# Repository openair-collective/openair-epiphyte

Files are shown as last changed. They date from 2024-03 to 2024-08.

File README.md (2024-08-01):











# Epiphyte

## Introduction

Epiphyte is a miniature, stand-alone, open source direct air capture machine that removes CO2 from the air, designed by OpenAir volunteers.

The name "Epiphyte" comes from the same term referring to a plant that grows on the surface of another plant. The "host plant" here is Thursday ([YouTube intro](https://www.youtube.com/watch?v=E_M0lsxscfE)), a previous generation carbon capture device designed by the team at Octavia Carbon of Kenya.

There are two main goals of the Epiphyte device:

1. __To reproduce Thursday in an alternate form in order to provide sufficient documentation to rebuild such a device.__ Thursday is an older generation carbon capture device. It is no longer in active development, and was to be used as an example to propagate build iterations in other locations. However, parts of Thursday still could not be disclosed, and the purpose of the Epiphyte build was to untangle very technical details of Thursday so that clear documentation can be created for next generation Thursday builders.

1. __To create a modular venue for testing sorbents.__ Although not a major purpose of Epiphyte, the recipe for Thursday cannot be disclosed exactly. Epiphyte is built so that the sorbent could be swapped out to study the behavior of different ones, if needed.

For further background information see the [links section](#links).

### Current state of the work

The original Epiphyte was built in Philadelphia, and University of Pennsylvania is home to it. The next potential steps depend on the data collected from this device, including:
- Heating and temperature control and feedback
- Carbon dioxide sensing--whether the current sensors are adequate
- Use of basic sorbents

From this data, knowledge of the mechanics of the device can be extracted. Depending on the ultimate goal of the device, i.e., research vs commercial vs "maker-ware", Epiphyte can be further improved, or elements of it can be borrowed in a completely new device.

## About this repository

This repository attempts to collect all relevant design files, documentation, and links, and presents them as a package of material that can be used to gain a viable amount of knowledge toward understanding the mechanics of Thursday.

The root folder has the following subdirectories:

```sh
.
├── hardware_files/
├── license_info/
├── presentations/
└── software/
```

### `presentations`

The PowerPoint presentations here include background information and schematics from throughout the build process. Schematics of the entire built system, photos of the build process, as well as preliminary data can be found throughout the slides.

If looking for an introduction to Epiphyte, looking at these presentations first is recommended.

### `license_info` and `LICENSE.txt`

The files in the folder explain how to use the material in this repository for further development. The technology is open-sourced (license text), but a few instructions (`license_info/cern_ohl_p_v2_howto.pdf`) need to be followed for material reuse.

### `software`

Includes Arduino code for controlling heating and reading from sensors on Epiphyte.

### `hardware`

This section has bills of materials (BOM) as well as a list of 3D components that can be used to create 3D assemblies. See the [hardware README](hardware_files/README.md) for more details and supplemental links.

## Links

#### YouTube videos

- [About Octavia Carbon's Thursday](https://www.youtube.com/watch?v=E_M0lsxscfE)
- [Live walkthrough of Thursday](https://www.youtube.com/watch?v=BNXJqeISVzQ)
- Epiphyte webinars
    - [Episode 1 - Intro and build launch](https://www.youtube.com/watch?v=B53BWDbAE4Q)
    - [Episode 2 - Assembly report](https://www.youtube.com/watch?v=-oX7TFdO3ws)
    - [Episode 3 - Sorbent panel progress](https://www.youtube.com/watch?v=SeYeDm23_dI)
    - [Epiphyte @ COP28](https://www.youtube.com/watch?v=A-t8T-azwP8)

#### Other

- [Epiphyte on OpenAir forums](https://www.openairforum.org/c/rd/epiphyte/106)
- [Epiphyte on Hackster.io](https://www.hackster.io/epiphyte/epiphyte-open-direct-air-capture-d55a9e)
- [First build on Carbon Crowd website](https://carboncrowd.cc/builds/vvRHB4d3vJyN1Ihpj5yi)

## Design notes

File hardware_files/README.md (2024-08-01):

# Hardware

## Hardware Description
The Hardware Description folder includes high-level documentation of how the parts are connected, as well as pinouts and engineering notes for different classes of components. Make sure to read [that documentation](HW%20Description/README.md) to see how the system is assembled. 

## Bills of Materials (BOMs)

A BOM is a list of materials needed to reproduce the physical device as closely as possible. There are two BOM files:

- Sorbent Panel and CO<sub>2</sub> Sensor Box
- Electronics and HVAC

Each list includes information on obtaining the materials, including vendors, pricing, whether customization is needed.

In the sorbent panel BOM, there are also a `Item ID` column that corresponds to individual 3D CAD files. There are two tabs in this file--one that lists off-the-shelf components (IDs that start with `M`), and the other that lists custom components (IDs that start with `C`).

### CAD files for sorbent panel and CO<sub>2</sub> sensor box components

3D CAD files for individual components, either in `.step` or `.sldprt` format, are available for most line items. These files include those for off-the-shelf components (for convenience) and custom components (required for repeat fabrication by a machine shop). The CAD file names are preceded by the `Item ID` so that they can be matched up to the line item easily. The anatomy of the CAD file names is as follows:

`{Item ID}_{Vendor Name}_{Part Number}_{Part Description}.{Extension}`

For custom parts, the file name is simply:

`{Item ID}_{Part Description}.{Extension}`

Some custom parts are provided with multiple formats of fabrication files, including 2D and 3D CAD files. 2D files may come in two versions--with and without holes--in case one wants to drill holes themselves, e.g., to save cost or for hole size flexibility.

CAD files of all custom parts are accessible, at the time of the publication of this repository, in live-maintained [Onshape](https://www.onshape.com/) files. The BOM lists links for finding the Onshape version of each custom file. The assemblies can be found here: [sorbent panel](https://cad.onshape.com/documents/3e513bed349fbe5dac3c2097/w/f4ba0cf31e493613401f5693/e/31d268d611fa49f66a7aafab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) and [sensor box](https://cad.onshape.com/documents/c282863293f77fd9e75ee4bd/w/2c50dc42efc36e588e65a721/e/b7f233adbe17413331fabfa8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)

Note: Onshape is free to use for non-commercial/hobby purposes. The files are free to access and download, although they may need an Onshape account to fork (in the same way software repos are forked).

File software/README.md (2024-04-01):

# Software

Software includes mainly Arduino code for controlling heating and sensors 
during capture of carbon.

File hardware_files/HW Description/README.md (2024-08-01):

# Epiphyte Electronic Hardware Description

## Overview
This document serves as a reference for the electronic hardware elements of the first prototype of Epiphyte. The design evolved as it was built, and I offer suggestions for improvement or modifications as appropriate.
In the interest of brevity, it is assumed that the reader is already familiar with electronics and programming.

### Epiphyte System
The overall design of the Epiphyte system is shown in Figure 1, below, with a focus on the elements to be described in this document.
 
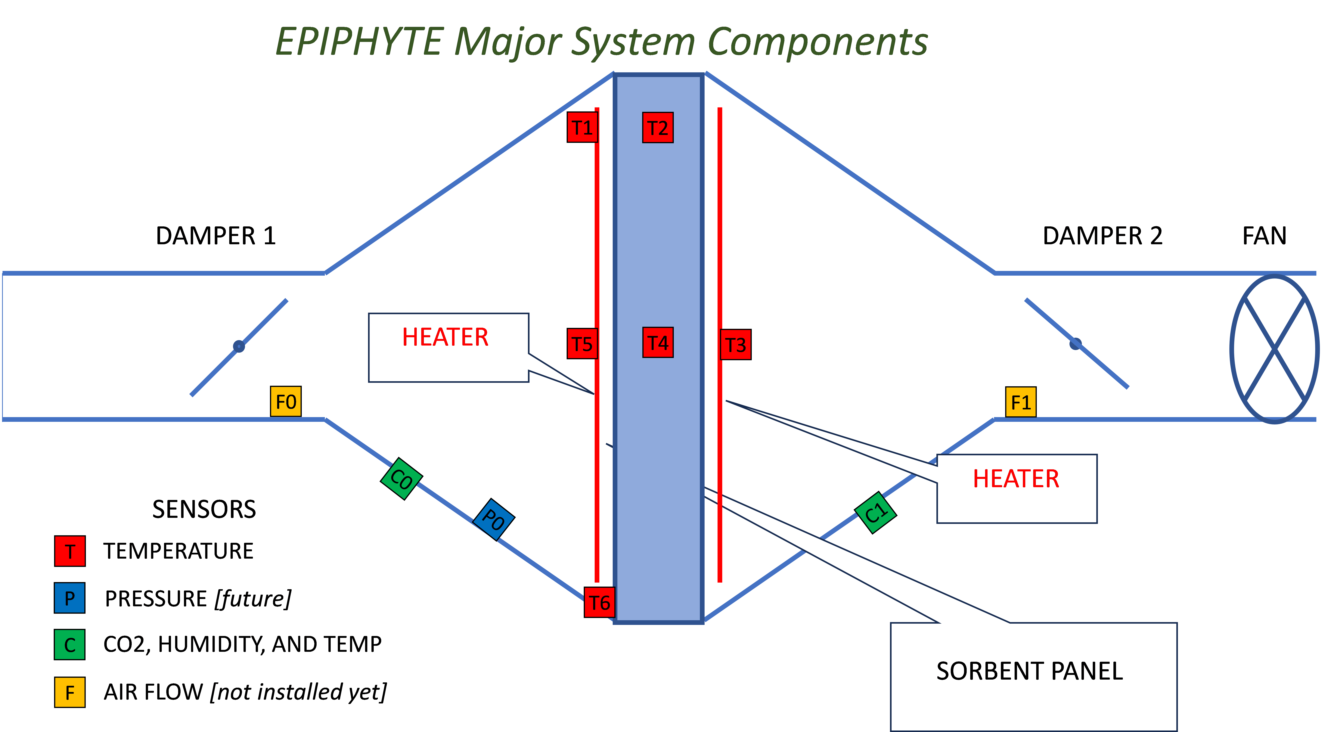
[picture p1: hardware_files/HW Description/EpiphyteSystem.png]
Epiphyte block diagram


### Electronics Block Diagram
To put the detailed description that follows into context, we include a high-level block diagram of Epiphyte’s electrical circuitry. 
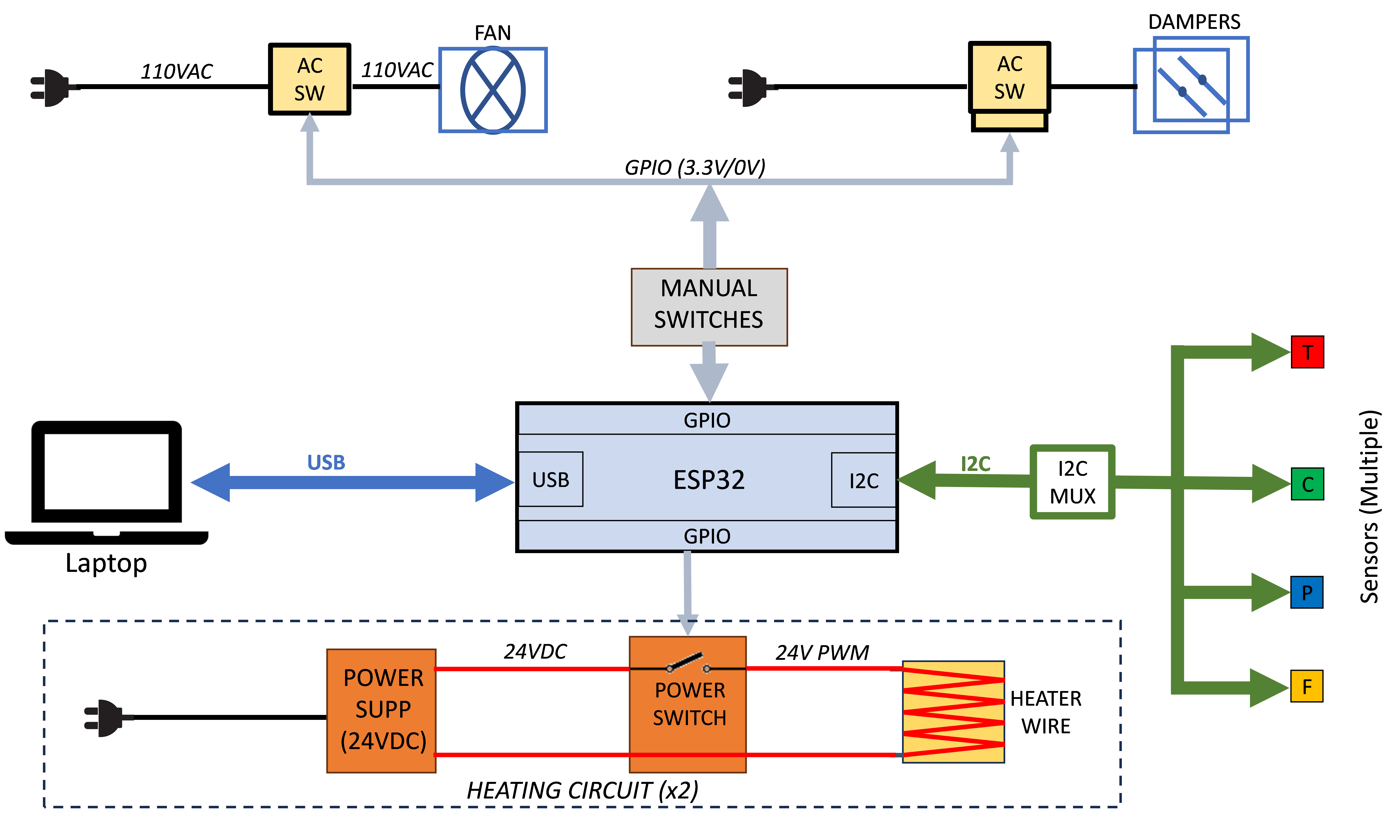
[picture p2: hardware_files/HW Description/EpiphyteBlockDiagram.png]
Epiphyte electrical block diagram


## Processor
The processor is an [Adafruit ESP32 Feather V2](https://www.adafruit.com/product/5400). Most other processors should work, as the application is not critical for speed or complex calculations. In particular, most 3.3-V processors of the Arduino or Adafruit Feather family should work with a few changes to the software. (Don’t use a 5V processor unless you know what you’re doing!) The processor also includes WiFi and Bluetooth connectivity, but these features have not been employed with Epiphyte as of this writing. They might be useful for data logging onto a server, or for remote control and monitoring of the system.

The user is urged to read and understand the information provided by Adafruit here: https://learn.adafruit.com/adafruit-esp32-feather-v2

The Feather can be programmed either in C/C++ or Python. In Epiphyte, I used C/C++.

### Pinout
Design files and pinouts for the board can be found here: https://github.com/adafruit/Adafruit-ESP32-Feather-V2-PCB/tree/main 
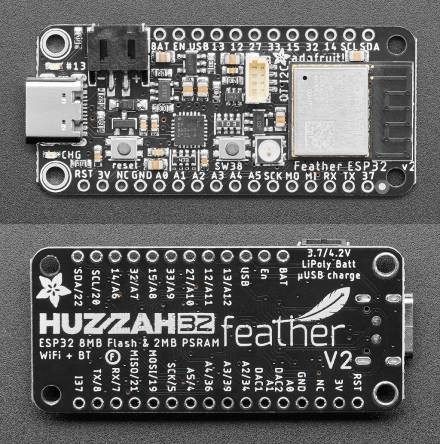
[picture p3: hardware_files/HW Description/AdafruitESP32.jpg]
Top and bottom of Adafruit ESP32 circuit board.
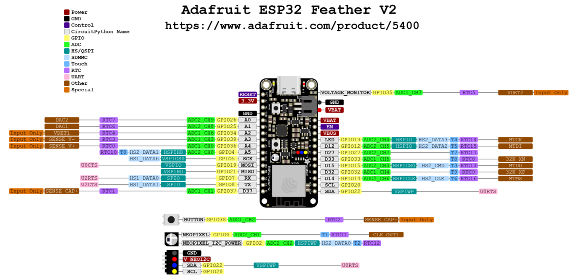
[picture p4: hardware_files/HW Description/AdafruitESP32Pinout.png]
Pinout diagram for Adafruit ESP32 circuit board.
 

### Display
For realtime monitoring of system activity, a monochrome OLED display is provided. This [Adafruit Featherwing](https://www.adafruit.com/product/4650) can be attached to the Feather processor. All connections are made through pins without needing any additional wiring. 
Communication with the display is via I2C, and this board also includes three pushbutton switches that are connected to processor GPIO pins. These could be useful for real-time control of the system.

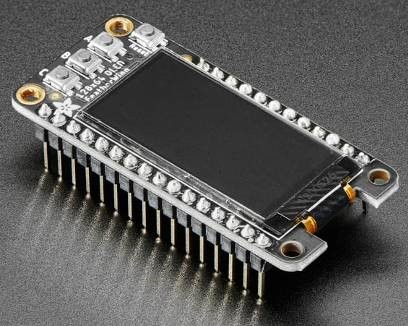
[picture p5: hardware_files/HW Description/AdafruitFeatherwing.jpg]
Image of Adafruit Featherwing OLED display.


### NeoPixel
An RGB LED (“Neopixel”) is supplied on the Feather board. This LED’s color and brightness can be programmed and used as a visual indicator. The NeoPixel library handles all the programming of this device.

### Processor Pin Assignments
This table shows the GPIO pins that are used in this design. Functions are detailed in sections below.
| Pin No | Signal | In/Out | Description |
|---|---|---|---|
| 0 | NEOPIXEL_PIN | O | Serial communication with NeoPixel |
| 12 | swRUN | I | To toggle switch: active LOW sets RUN mode |
| 13 | swSET | I | To toggle switch: active LOW sets SETUP mode |
| 14 | BUTTON_C | I | To OLED board pushbutton C (not used) |
| 15 | BUTTON_A | I | To OLED board pushbutton A (not used) |
| 27 | HEAT_PWM_1 | O | To Heater 1 control gate; PWM duty-cycle control |
| 32 | BUTTON_B | I | To OLED board pushbutton A (not used) |
| 33 | HEAT_PWM_2 | O | To Heater 2 control gate; PWM duty-cycle control |

## I2C Connections
The sensors in Epiphyte are all connected to the processor with the [I2C](https://en.wikipedia.org/wiki/I%C2%B2C) serial bus.  It is important to note that because the processor supply and interfaces are 3.3V, any slave devices must also operate from this voltage (including pullups) to avoid damaging the processor.

### Stemma QT
[STEMMA QT](https://learn.adafruit.com/introducing-adafruit-stemma-qt/what-is-stemma-qt) is an Adafruit system for easily making I2C connections between compatible devices. Many boards come with a STEMMA QT connector, and cables of various lengths are available to connect devices simply by plugging in the cables. 
Each cable has 4 wires: Power, Ground, SDA, and SCK. Cables come in various lengths; an example is depicted below.
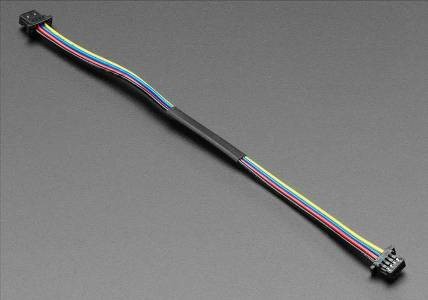
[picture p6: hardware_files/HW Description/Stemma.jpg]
Photograph of Adafruit Stemma QT cable.


### I2C Extender
I2C signals suffer degradation with longer cables (including STEMMA QT cables). The [I2C extender](https://www.adafruit.com/product/4756) allows cascades of STEMMA QT cables or longer runs between the processor and the sensors. The LTC4311 is an IC which boosts and reshapes I2C signals, and is available from Adafruit on a breakout board with convenient STEMMA QT connectors. This device is liberally used in Epiphyte wherever longer signal runs are needed.
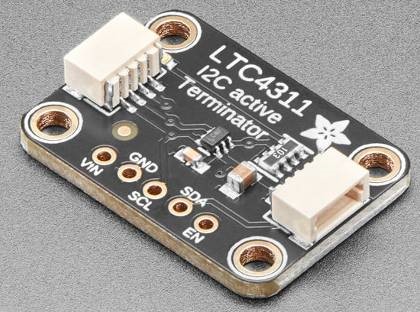
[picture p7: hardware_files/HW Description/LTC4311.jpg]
Adafruit LTC4311 I2C Extender breakout board.


### I2C Multiplexing
Because there are multiple instances of each type of sensor, most with fixed I2C addresses, a multiplexer is necessary to disambiguate these devices for correct addressing. Adafruit makes a [breakout board](https://www.adafruit.com/product/5626) for the PCA9548 I2C multiplexer chip (shown below), which features a common port on the end and eight switched ports around two edges, all with STEMMA QT connectors.

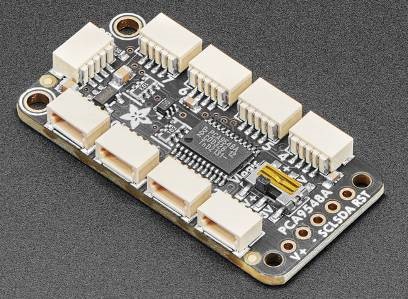
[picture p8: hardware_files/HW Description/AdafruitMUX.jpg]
Photograph of Adafruit 1:8 mux.


The MUX acts as a bidirectional 1-to-8 switch, and is itself an I2C device with its own address. The I2C address of the MUX can be selected with solderable jumpers on the PCB (labelled A0, A1, and A2 on the back - see image below). The position of the switch is controlled by the processor sending a formatted command. Then the MUX becomes transparent and the selected slave device can be addressed in the usual way as if it were the only one on the bus with that address. Note that the ports are numbered 0 through 7.

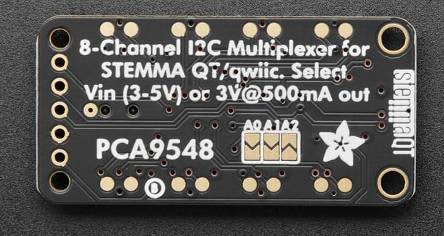
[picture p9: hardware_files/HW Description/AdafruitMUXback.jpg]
Photograph of Adafruit 1:8 mux breakout board, back side.


In the current embodiment of Epiphyte, two 1:8 MUXes are used, with labels as used in the software and corresponding addresses as follows:
| MUX Label | MUX I2C Address |
|---|---|
| MUX1 | 0x71 |
| MUX2 | 0x72 |

The MUX addresses and port numbers of each sensor used in Epiphyte are shown in this table and in the schematic below:
| Device | Part No. | Label | MUX# | MUX Channel | Device I2C Address | Location |
|---|---|---|---|---|---|---|
| Thermocouple Amp | MCP9600 | T0 | 2 | 0 | 0x67 | Not used |
| Thermocouple Amp | MCP9600 | T1 | 2 | 1 | 0x67 | Input side heater wire, corner |
| Thermocouple Amp | MCP9600 | T2 | 2 | 2 | 0x67 | Sorbent center, corner |
| Thermocouple Amp | MCP9600 | T3 | 2 | 3 | 0x67 | Output side heater wire, center |
| Thermocouple Amp | MCP9600 | T4 | 2 | 4 | 0x67 | Sorbent center, center |
| Thermocouple Amp | MCP9600 | T5 | 2 | 5 | 0x67 | Input side heater wire, center |
| Thermocouple Amp | MCP9600 | T6 | 2 | 6 | 0x67 | Sorbent frame |
| Thermocouple Amp | MCP9600 | T7 | 2 | 7 | 0x67 | Not used |
| CO2 Sensor | SCD30 | C0 | 1 | 3 | 0x61 | Input duct |
| CO2 Sensor | SCD30 | C1 | 1 | 4 | 0x61 | Output duct |
| Pressure Sensor | MPRLS | P0 | 1 | 5 | 0x18 | Not used (yet) |
| Flow meter | FS1015-1005 | F0 | 1 | 2 | 0x50 | Not used (yet) |
| Flow meter | FS1015-1005 | F1 | 1 | 1 | 0x50 | Not used (yet) |

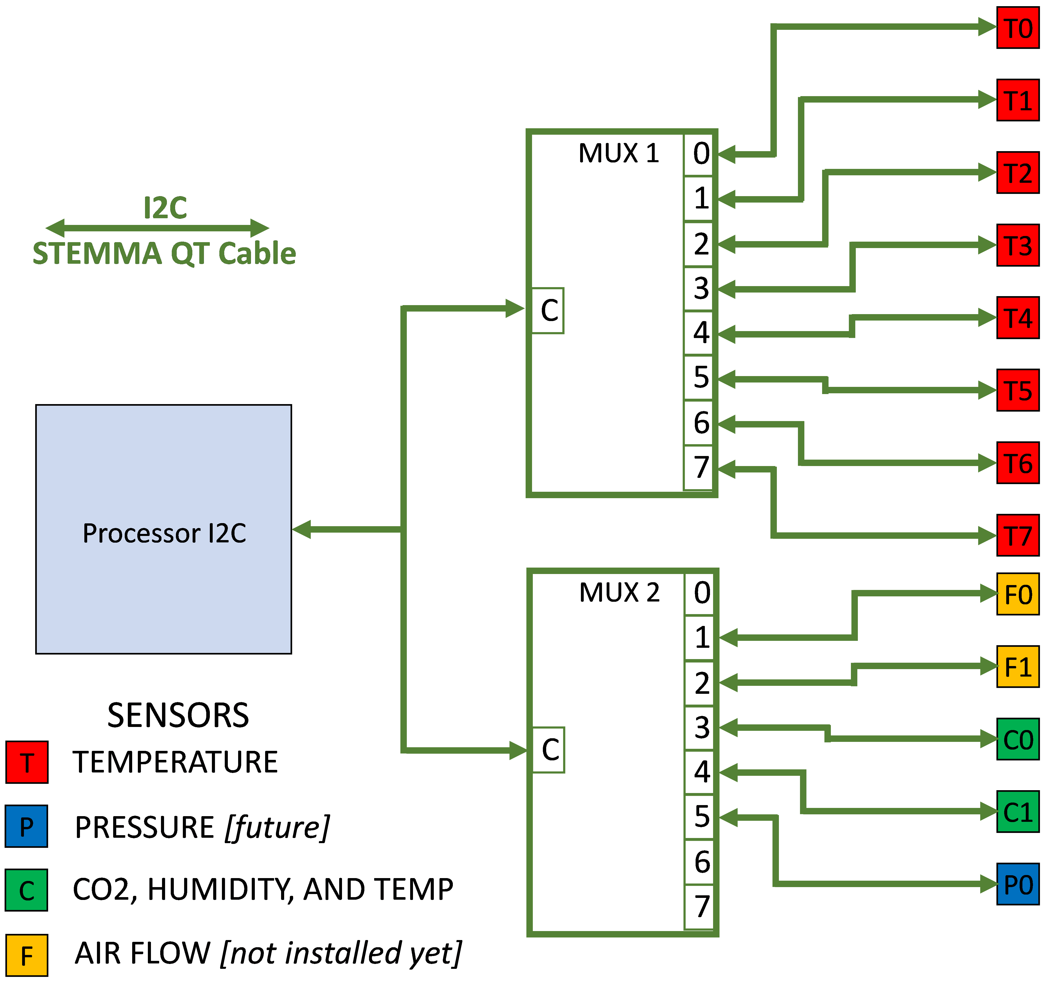
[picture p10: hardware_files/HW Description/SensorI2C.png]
Schematic of sensor I2C connectivity.

Note one simplification made in this diagram: For connecting the Airflow Sensors, which require a 5-V power supply, a Logic Level Shifter is required to shift the 3.3-V I2C levels to the 5-V system.

### Logic Level Shifter
The [logic level shifter](https://www.adafruit.com/product/757) is pretty flexible in that it can shift logic levels between any two voltages that are supplied to it. In Epiphyte, pin “LV” is connected to 3.3V, and the I2C SDA and SCL lines from the MUX that control the Airflow Sensors are connected to pins A1 through A4; “HV” is powered from 5V (from the Feather USB pin) and pins B1 through B4 go to the I2C pins of the two Airflow Sensors.
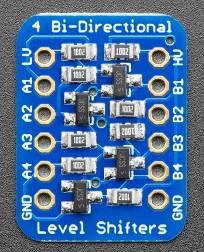
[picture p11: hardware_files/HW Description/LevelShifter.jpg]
Photograph of Adafruit level shifter board.


## Control Switches
A number of toggle switches are provided for manually controlling the state of the executing software and to control the fan and dampers. These switches are all SPDT (single-pole/double throw). They are connected as follows:
| Name | Common | Term 1 | Term 2 | Function |
|---|---|---|---|---|
| POWER | GND | EN | N/C | Powers up processor |
| RUN/SET | GND | Pin 12; pullup | Pin 13; pullup | RUN=normal system function SET=configure system parameters via terminal |
| FAN | Fan relay | GND | Pullup | Activates fan |
| DAMPER | Damper relay | GND | Pullup | Activates dampers |

Note: [pullups](https://en.wikipedia.org/wiki/Pull-up_resistor), where indicated, are 10kohm to 3.3V.

There is also a pushbutton connected to the processor RESET pin. This is redundant with the RESET button on the processor, but provided for ergonomic reasons.

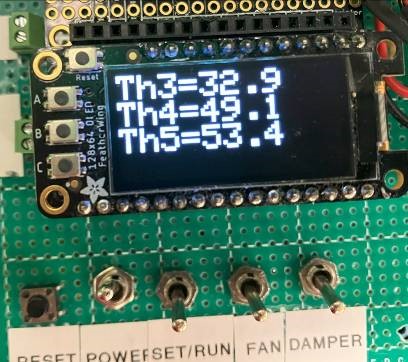
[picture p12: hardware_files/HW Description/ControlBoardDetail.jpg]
Photograph of Adafruit level shifter board.
.

## Heating System
Two heating systems are supplied, one for each side of the sorbent. The details of this system will vary greatly depending on the amount of heat needed by the sorbent, the location of the wires, the heat loss from parasitic conduction, and the size of the sorbent panel.

Based on estimates from various sources, I concluded that a maximum power capability of 240W for each system would be sufficient:

*P* = *D* \* *V*<sup>2</sup>/*R*

### Nichrome Wires
The wires used have a resistivity of 0.4 ohm/ft. The total length of each heater element is 6 ft, yielding a resistance of 2.4 ohm.
https://www.digikey.com/en/products/detail/remington-industries/18N8025/11612571

### Power Supply
The power supply needs to produce at least 240 W. This unit does nicely:
https://www.amazon.com/MEAN-WELL-LRS-350-24-350-4W-Switchable/dp/B013ETVO12/ref=sr_1_3
At an output voltage of 24V, the maximum current drawn by the heating wire would be 10A.
The two supplies were mounted in a closed chassis for safety:

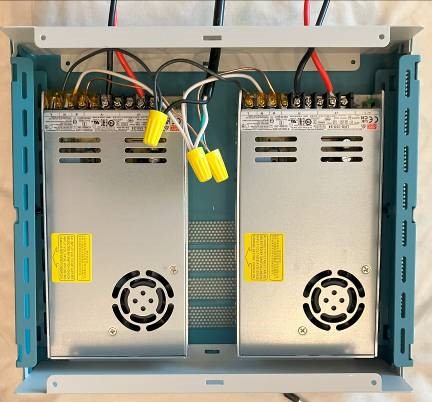
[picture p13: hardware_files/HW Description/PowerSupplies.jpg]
Dual heater power supplies.
.

### PWM Switching Circuit
The circuit diagram for each switching circuit is shown as an LTSpice schematic here:

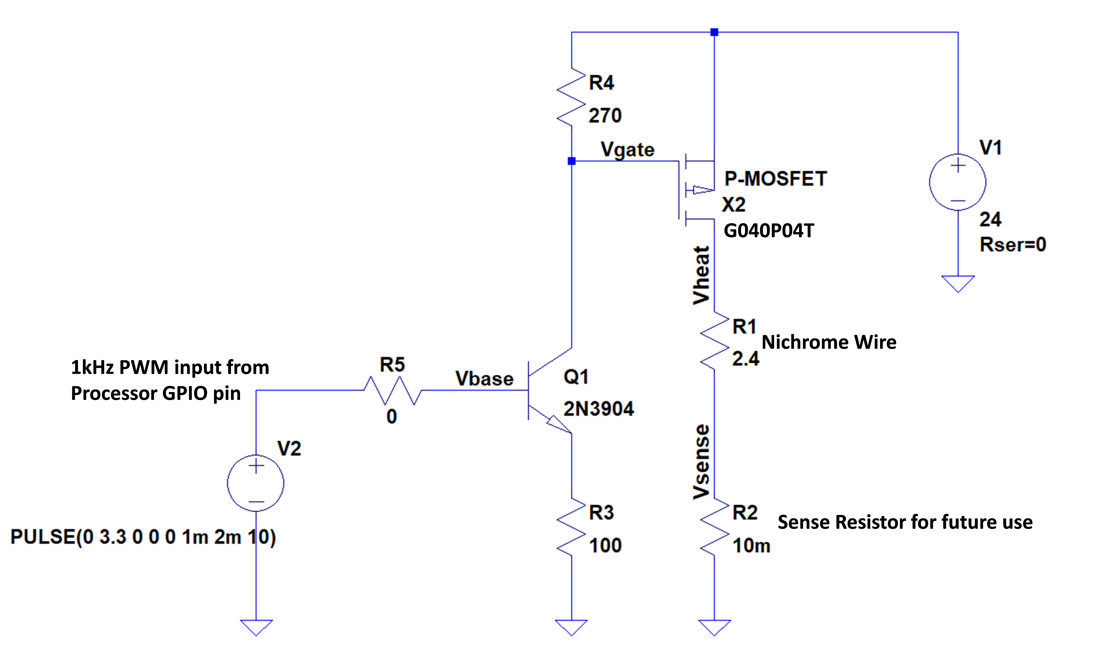
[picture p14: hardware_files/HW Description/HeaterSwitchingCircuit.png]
Heater switching circuit


V1 represents the 24-VDC power supply; V2 is the 1-kHz PWM switching signal from the processor pin, and R1 represents the 2.4-ohm resistance of the nichrome wire. The simulation accurately predicted the performance of the actual circuit.

## Mechanical Controls
### Fan
The [fan](https://hvacquick.com/products/residential/AirFlow-Boosting/Inline-Air-Booster-Fans/AC-Infinity-CLOUDLINE-Inline-Fans-With-Speed-Controller) requires an AC power supply. A digitally controlled AC relay turns the power on or off; currently this relay is controlled by a manual toggle switch but this could also be connected to a processor GPIO pin for progam control.
The fan also has a control switch with a pushbutton to adjust the fan speed. At the time of writing, this is done manually. More research needs to be done to work out how to control the fan speed under processor control.

### Dampers
This [damper](https://hvacquick.com/products/residential/Zoning-and-Zone-Dampers/Zone-Dampers/Suncourt-Motorized-Zone-Dampers) is Normally Open. Applying 24VAC closes the flapper. A transformer is supplied to reduce the 110VAC line voltage to the correct operating level. As with the Fan, an AC relay is used to activate the dampers, also controlled by a manual switch for the time being. To save on parts, both dampers are controlled together from one switch.

### AC Relays
This [relay](https://www.amazon.com/gp/product/B00WV7GMA2/ref=ppx_yo_dt_b_asin_title_o00_s00) switches an AC line voltage between outlets under DC control. 

## Sensors
### CO2 Sensors
The Sensirion SCD30 CO2 sensor is employed in Epiphyte. It is available on a [breakout board from Adafruit](https://www.adafruit.com/product/4867), with STEMMA QT connectors.
**NOTE:** the sensor may work fine as-is, but the design of this breakout board is deficient: the SCD30 sensor requires a minimum of 3.3V for specified operation, but this board, which nominally has a 3.3V supply input from the STEMMA QT cable, actually supplies a lower voltage due to drops in the LDO and wire resistance. For reliable operation, I found it necessary to bypass the LDO, and connect the input supply and ground directly to the processor with heavier wires (22 AWG was fine).

### Temperature Sensors and Amplifiers
Two types of thermocouples were used, with no real difference between them except the shape of the sensor element:
[Thermocouple Type-K Glass Braid Insulated Stainless Steel Tip](https://www.adafruit.com/product/3245) and [Thermocouple Type-K Glass Braid Insulated - 5m](https://www.adafruit.com/product/3895)
It is important to note that the sensor end of either type of thermocouple is not electrically insulated, so if it is contacting a conductive surface, it must be insulated from it. Kapton tape works well for this.
These thermocouples respond with a very low voltage, so an amplifier is needed. The MCP9600, available on a [breakout from Adafruit](https://www.adafruit.com/product/4101), amplifies and digitizes the signal so it can be read with I2C.

### Pressure Sensors (not implemented)
We specified [pressure sensors](https://www.adafruit.com/product/3965), but at the time of writing this device has not been used. 

### Airflow Sensors
https://www.mouser.com/ProductDetail/972-FS10151005
Note: this part is shown as “obsolete” so a replacement will need to be found.

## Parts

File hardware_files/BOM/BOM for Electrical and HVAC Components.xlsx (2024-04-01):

Item # | Sorbent
 | Item | Supplier | Part Number | Order Link | Quantity | Units | Unit Cost | Total Cost | Comment
1 | Molecular sieves, 13X, 1.6mm pellets | Sigma Aldrich | 334340 | https://www.sigmaaldrich.com/US/en/product/sigald/334340 | 2 | 1-kg bottle | $165.00 | $330.00 | Recommend a different sorbent material for TVSA of CO2
 |  |  |  |  |  |  | Total | $330.00
 | Sorbent Chamber
 | Item | Supplier | Part Number | Order Link | Quantity | Units | Unit Cost | Total Cost | Comment
11 | HVACQuick CFB series inline filter box. For 10 inch ducts. | HVACQuick | CFB-10 | https://www.hvacquick.com/products/residential/Air-Filters/Inline-Filter-Boxes/HVACQuick-CFB-Series-MERV-13-Inline-Filter-Boxes | 1 | Ea. | $249.00 | $249.00 | Intended for HVAC systems; it is made of thin aluminum and needs to be sturdier and more airtight for the next build.
12 | AC Infinity CLOUDLINE S10 inline fan. For 10 inch duct. Includes corded (20 foot) speed controller. 1201 CFM. | HVACQuick (AC Infinity) | CLS10 (AI-CLS10) | https://hvacquick.com/products/residential/AirFlow-Boosting/Inline-Air-Booster-Fans/AC-Infinity-CLOUDLINE-Inline-Fans-With-Speed-Controller | 1 | Ea. | $269.00 | $269.00 | Could use two (one at each end) if more airflow is required.
13 | Suncourt On/Off adjustable zone control damper. 10 inch round. NORMALLY OPEN. 24 VAC. Plug-in 120V to 24V transformer included. | HVACQuick (Suncourt) | ZO210 | https://hvacquick.com/products/residential/Zoning-and-Zone-Dampers/Zone-Dampers/Suncourt-Motorized-Zone-Dampers | 2 | Ea. | $93.99 | $187.98 | This is a fire damper for home/commercial HVAC systems. Not airtight enough for vacuum operation.
14 | Uline Flat Shelf Utility Cart - 44 x 25 x 33" - BLACK | ULINE | H-3325BL | https://www.uline.com/Product/Detail/H-3325BL/Utility-Carts/Uline-Flat-Shelf-Utility-Cart-44-x-25-x-33-Black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 | 1 | Ea. | $170.00 | $170.00 | For mounting and transporting Epiphyte.
15 | 10 in. Round Duct Cap | Home Depot (Masterflow) | DC10 | https://www.homedepot.com/p/Master-Flow-10-in-Round-Duct-Cap-DC10/203612782 | 2 | Ea. | $17.93 | $35.86 | Not used. Was intended for use if dampers did not work.
 |  |  |  |  |  |  | Total | $911.84
 | Control Electronics & Sensors
 | Item | Supplier | Part Number | Order Link | Quantity | Units | Unit Cost | Total Cost | Comment
21 | Processor: Adafruit ESP32 Feather V2 (STEMMA QT) | Adafruit | 5400 | https://www.adafruit.com/product/5400 | 1 | Ea. | $19.95 | $19.95 | Includes WiFi and Bluetooth LE. Go to product page links for tutorials, description, and IDE instructions.
22 | USB Cable: Type A to Type C, 1 meter | Adafruit | 4474 | https://www.adafruit.com/product/4474 | 1 | Ea. | $4.95 | $4.95
23 | Feather tripler board | Adafruit | 3417 | https://www.adafruit.com/product/3417 | 1 | Ea. | $8.50 | $8.50 | Accomodates up to 3 Feather form factor devices; e.g. Feather, Display, and spare slot
24 | FeatherWing OLED - 128x64 OLED Add-on For Feather | Adafruit | 4650 | https://www.adafruit.com/product/4650 | 1 | Ea. | $14.95 | $14.95 | 4-line display; can be mounted on Tripler board or connected with STEMMA QT cable.
25 | PCA9548 8-Channel STEMMA QT / Qwiic I2C Multiplexer | Adafruit | 5626 | https://www.adafruit.com/product/5626 | 2 | Ea. | $6.95 | $13.90 | Allows up to 8 devices to operate with shared I2C slave address.
26 | LTC4311 I2C Extender / Active Terminator | Adafruit | 4756 | https://www.adafruit.com/product/4756 | 6 | Ea. | $7.50 | $45.00 | Used where needed to extend run of STEMMA QT I2C connection
27 | CO2 Sensor: (Sensirion) SCD-30 - NDIR CO2 Temperature and Humidity Sensor (STEMMA QT) | Adafruit | 4867 | https://www.adafruit.com/product/4867 | 2 | Ea. | $58.95 | $117.90 | Adafruit's breakout board for the SCD30. I recommend bypassing the STEMMA 3.3V and GND lines with separate, thicker leads; and bypassing the board's LDO. Otherwise the supply voltage to the SCD30 is too low and it gets flaky.
28 | Air Flow Sensor | Renesas | FS1015-1005 | https://www.mouser.com/ProductDetail/972-FS10151005 | 2 | Ea. | $26.72 | $53.44 | Tested but not integrated with Epiphyte system.
29 | Thermocouple Type-K Glass Braid Insulated, standard tip | Adafruit | 270 | https://www.adafruit.com/product/270 | 4 | Ea. | $9.95 | $39.80 | Use combination of this one or the one below, depending on which makes the best thermal contact. Tip must be electrically insulated from system.
30 | Thermocouple Type-K Glass Braid Insulated, Stainless Steel Tip | Adafruit | 3245 | https://www.adafruit.com/product/3245 | 4 | Ea. | $9.95 | $39.80 | See above.
31 | MCP9600 I2C Thermocouple Amplifier | Adafruit | 4101 | https://www.adafruit.com/product/4101 | 8 | Ea. | $15.95 | $127.60 | Required for interfacing thermocouple with I2C.
32 | MPRLS Ported Pressure Sensor Breakout - 0 to 25 PSI | Adafruit | 3965 | https://www.adafruit.com/product/3965 | 2 | Ea. | $14.95 | $29.90 | Not used yet in Epiphyte, so hasn't been tested.
33 | Logic Level Converter Breakout, 4 channel | Adafruit | 757 | https://www.adafruit.com/product/757 | 1 | Ea. | $3.95 | $3.95 | Flow sensor requires 5-V supply and hence 5-V I2C interface. This device converts I2C signal between 3.3V and 5V.
34 | Digitally-controlled AC relay ("IOT Relay") | Digital Loggers, Inc. | N/A | https://dlidirect.com/products/iot-power-relay | 2 | Ea. | $29.00 | $58.00 | TTL-controled AC relay, works with 3.3V. For activating fan and dampers.
 |  |  |  |  |  |  | TOTAL | $577.64
 | Sorbent Heater System
 | Item | Supplier | Part Number | Order Link | Quantity | Units | Unit Cost | Total Cost | Comment
51 | DIY Electronic Enclosure Box Case 1.5U 65 x 279 x 305 mm. | Cheval Electronic Enclosure Co.,Ltd | B09MK3TSGR | https://www.amazon.com/Electronic-Enclosure-Case-1-5U-Aluminum/dp/B09MK3TSGR/ref=sr_1_4 | 1 | Ea. | $26.26 | $26.26 | Generic electrical box to safely isolate the 120-V AC line inputs to the two 24-V power converters. May not be needed depending on converters chosen.
52 | Power supply--AC In, 24VDC 14.6A Out | Meanwell | LRS-350-24 | https://www.amazon.com/MEAN-WELL-LRS-350-24-350-4W-Switchable/dp/B013ETVO12/ref=sr_1_3 | 2 | Ea. | $31.45 | $62.90 | Generic power supply. May be able to reduce size or use only one depending on sorbent heating needs and thermal efficiency of panel.
53 | Nichrome wire: 25ft, 18AWG | Remington | 18N8025 | https://www.digikey.com/en/products/detail/remington-industries/18N8025/11612571 | 1 | Spool | $20.14 | $20.14 | May need more or less depending on heater design, or a different size wire. BARE so may need insulating jacket or other means of electrical isolation if wire contacts metal panel.
54 | Fiberglass sleeve for wire-0.051" ID, 100-ft length | AlphaWire | PF24016 NA005 | https://www.digikey.com/en/products/detail/alpha-wire/PF24016-NA005/3843442 | 1 | Spool | $49.89 | $49.89 | See above. Need depends on whether heater wire contacts metal. It would be best to do without this as it blocks some of the heat flow to the sorbent.
55 | Sense resistor for current monitor--0.01 ohm, 1%, 5W | Riedon | MSR5-0R01F1 | https://www.digikey.com/en/products/detail/riedon/MSR5-0R01F1/1641093 | 2 | Ea. | $1.41 | $2.82 | Current sense circuit has not been tested.
56 | Op-Amp for current monitor. 8-pin DIP, precision | Analog Devices | LT1677CN8#PBF | https://www.digikey.com/en/products/detail/analog-devices-inc/LT1677CN8-PBF/962980 | 2 | Ea. | $6.72 | $13.44 | Current sense circuit has not been tested.
57 | MOSFET, P-channel | Goford Semi | G040P04T | https://www.digikey.com/en/products/detail/goford-semiconductor/G040P04T/19524542 | 2 | Ea. | $1.91 | $3.82 | Current Switch for PWM heater control circuit. Gate driven by NPN transistor (below)
58 | Bipolar Transistor, NPN | OnSemi | 2N3904BU | https://www.digikey.com/en/products/detail/onsemi/2N3904BU/1413 | 2 | Ea. | $0.35 | $0.70 | Base driven by GPIO. Generic type--many substitutions available
59 | Wire nuts assortment | Various |  | https://www.amazon.com/Electrical-Connectors-Colorful-Assortment-Connection/dp/B09NRFGTDH/ref=sr_1_3 | 1 | Kit | $9.99 | $9.99 | Just an example. Available online or from any hardware store.
60 | Screw terminal--Wire to board | Amphenol | VP0265540000G | https://www.digikey.com/en/products/detail/amphenol-anytek/VP0265540000G/4957847 | 4 | Ea. | $2.60 | $10.40 | For connecting high-current wires to hand-built heater driver board.
61 | Hookup wire, red and black--10ft, 12AWG | Generic |  | https://www.amazon.com/Electrical-Silicone-Flexible-temperature-resistance/dp/B0756TDTDM/ref=sr_1_9 | 1 | Ea. | $11.98 | $11.98 | For connecting 24-V supply to heater driver, and heater driver to heating wires.
62 | Power cord with switch, 6 ft, 18AWG | Generic |  | https://www.amazon.com/gp/product/B07VQK3ZVK/ref=ppx_od_dt_b_asin_title_s00?th=1 | 1 | Ea. | $14.99 | $14.99 | Supply cord for heater power converters to allow shutoff
63 | Thermistor PTC 100 ohm | TDK |  | https://www.digikey.com/en/products/detail/epcos-tdk-electronics/B59100M1170A070/651876 | 4 | Ea. | $6.67 | $26.68 | Not used yet in Epiphyte, so hasn't been tested. Intent is to shut down heater drive circuit if wire gets too hot.
 |  |  |  |  |  |  | TOTAL | $254.01
 | Generic electronics items
 | Item | Supplier | Part Number | Order Link | Quantity | Units | Unit Cost | Total Cost | Comment
71 | Hook-up Wire Spool Set - 22AWG Solid Core - 6 x 25 ft | Adafruit |  | https://www.adafruit.com/product/1311 | 1 | Set | $15.95 | $15.95 | Assorted colors; for general use interconnecting low-power circuits.
72 | STEMMA QT Cable--400mm long | Adafruit |  | https://www.adafruit.com/product/5385 | 12 | Ea. | $1.50 | $18.00 | 4-wire I2C/power cable, with connector.
73 | STEMMA QT Cable--100mm long | Adafruit |  | https://www.adafruit.com/product/4210 | 8 | Ea. | $0.95 | $7.60 | 4-wire I2C/power cable, with connector.
74 | STEMMA QT Cable to 4 male headers | Adafruit |  | https://www.adafruit.com/product/4209 | 10 | Ea. | $0.95 | $9.50 | 4-wire I2C/power cable, with connector.
75 | STEMMA QT Cable to 4 female sockets | Adafruit |  | https://www.adafruit.com/product/4397 | 6 | Ea. | $0.95 | $5.70 | 4-wire I2C/power cable, with connector.
76 | STEMMA QT / Qwiic JST SH 4-Pin Cable - 50mm Long | Adafruit |  | https://www.adafruit.com/product/4399 | 4 | Ea. | $0.95 | $3.80 | 4-wire I2C/power cable, with connector.
77 | Resistor Kit--Generic (Example shown) | Geekstory |  | https://www.amazon.com/Precision-Electronic-Assortment-1ohm-1Mohm-Geekstory/dp/B079FP5WD9/ref=sr_1_1 | 1 | Kit | $13.99 | $13.99 | 1/4-W, 1% Leaded Resistor Kit, 1460pcs, 73 values. Any available resistor kit will do that contains the values needed.
78 | Perfboard | Generic |  | https://www.amazon.com/gp/product/B07VHNHMMJ/ref=ppx_yo_dt_b_asin_title_o03_s01 | 1 | Kit | $9.99 | $9.99 | Just an example. Use any preferred system for mounting hand-wired electronics.
79 | Screw terminals | Generic |  | https://www.amazon.com/gp/product/B09BVF5B28/ref=ppx_yo_dt_b_asin_title_o00_s00 | 2 | Kit | $6.99 | $13.98 | Wire to breadboard connectors
80 | Proto Boards--10 pack, assorted sizes | Generic |  | https://www.amazon.com/gp/product/B0CBPRKDRR/ref=ppx_yo_dt_b_asin_title_o08_s00 | 1 | Pkg | $11.49 | $11.49 | Example. For constructing electronics.
81 | Adafruit Perma-Proto Half-sized Breadboard, 3pcs | Adafruit | 571 | https://www.adafruit.com/product/571 | 1 | Pkg | $12.50 | $12.50 | Breadboard
 |  |  |  |  |  |  | TOTAL | $122.50
 | Miscellaneous Tools and Equipment
 | Item | Supplier | Part Number | Order Link | Quantity | Units | Unit Cost | Total Cost | Comment
91 | Oscilloscope | Multiple | Generic | N/A
92 | Multimeter | Multiple | Generic | N/A
93 | Soldering iron | Multiple | Generic | N/A
94 | Heat gun | Multiple | Generic | N/A
95 | Power strips | Multiple | Generic | N/A
96 | Drill | Multiple | Generic | N/A
97 | Screwdrivers (manual or electric) | Multiple | Generic | N/A
98 | SURAILEC Watt Meter | Amazon |  | https://www.amazon.com/gp/product/B08GSPLZBN/ref=ppx_od_dt_b_asin_title_s00?ie=UTF8&psc=1 | 1 | Ea. | $27.98 | $27.98 | For measuring system power consumption
99 | Assark Glue Gun, Mini Hot Glue Gun Kit | Amazon |  | https://www.amazon.com/dp/B09FYWQ44L?ref=ppx_yo2ov_dt_b_product_details&th=1 | 1 | Ea. | $8.48 | $8.48 | For sealing cracks and holes
 |  |  |  |  |  |  | TOTAL | $36.46 | Not including generic items w/o ordering info
 | Materials and Hardware
 | Item | Supplier | Part Number | Order Link | Quantity | Units | Unit Cost | Total Cost | Comment
111 | Sheet Metal Screws | Various | Generic |  |  |  |  |  | For connecting flanges of fan-damper-chamber assembly
112 | Solder | Various | Generic |  |  |  |  |  | Lead-free preferred
113 | Rubber grommet kit | Amazon |  | https://www.amazon.com/gp/product/B0C9GRF1S3/ref=ppx_od_dt_b_asin_title_s00 | 1 | Kit | $8.99 | $8.99 | For feeding wires through holes in sheet metal
114 | Nylon threaded spacer kit | Amazon |  | https://www.amazon.com/gp/product/B07TP2YYQB/ref=ppx_od_dt_b_asin_title_s00?ie=UTF8&th=1 | 1 | Kit | $14.88 | $14.88 | For constructing electronics.
115 | 300-piece M2 Philips Head Screw kit | Generic |  | https://www.amazon.com/gp/product/B01NBOD98K/ref=ppx_od_dt_b_asin_title_s00?ie=UTF8&psc=1 | 1 | Ea. | $27.98 | $8.97 | For constructing electronics.
116 | Kapton tape | Various | Generic
117 | Heat-shrink tubing | Various | Generic
118 | Standoffs Kit, 3M, assorted | Generic |  | https://www.amazon.com/LitOrange-Standoff-Threaded-Motherboard-Assortment/dp/B07TP2YYQB/ref=sr_1_4 | 1 | Ea. | $14.88 | $14.88 | For constructing electronics.
119 | Nylon Standoffs kit, 2M size | Generic |  | https://www.amazon.com/gp/product/B07XZ3MMHB/ref=ppx_od_dt_b_asin_title_s00 | 1 | Pkg | $8.58 | $8.58 | Example. For mounting electronics
120 | Clear Silicone RTV Gasket Maker and Silicone Sealant | ABRO |  | https://www.amazon.com/dp/B00IOOAB6C?psc=1&ref=ppx_yo2ov_dt_b_product_details | 1 | Ea. | $9.99 | $9.99
 |  |  |  |  |  |  | TOTAL | $66.29 | Not including generic items w/o ordering info
 |  |  |  |  |  |  | Grand Total: | $2298.74

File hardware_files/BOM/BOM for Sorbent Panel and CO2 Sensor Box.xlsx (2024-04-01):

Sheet: Off-shelf components
Item ID | CAD Available? | Description | Quantity | Size | Supplier | Part # | Link | Supplier Quantity | Unit Cost | Total Cost | Notes
M1 | Y | T-slot frame 24 | 2 | 23 3/4 inches | 8020 | 1515-ULS | https://8020.net/1515-uls.html |  | $16.56 | $33.12 | Each piece includ $2.79 surcharge per cut; can also obtain from https://www.mcmaster.com/47065T102 but length is less customizable
M2 | Y | T-slot frame 21 | 4 | 21 inches | 8020 | 1515-ULS | https://8020.net/1515-uls.html |  | $14.97 | $59.88 | Each piece includ $2.79 surcharge per cut; can also obtain from https://www.mcmaster.com/47065T102 but length is less customizable
M3 | Y | T-slot frame 8 | 2 | 8 inches | 8020 | 1515-ULS | https://8020.net/1515-uls.html |  | $7.43 | $14.86 | Each piece includ $2.79 surcharge per cut; can also obtain from https://www.mcmaster.com/47065T102 but length is less customizable
M4 | Y | T-slot offsets | 4 | 2.5 inches | 8020 | 1515-ULS | https://8020.net/1515-uls.html |  | $4.24 | $16.96 | Each piece includ $2.79 surcharge per cut; can also obtain from https://www.mcmaster.com/47065T102 but length is less customizable
M5 | Y | Frame L-brackets | 12 |  | 8020 | 4302 | https://8020.net/4302.html |  | $4.41 | $52.92
M5 | Y | Front/Back Plate L-Brackets | 16 |  | 8020 | 4302 | https://8020.net/4302.html |  | $4.41 | $70.56
M5 | Y | L-brackets -offsets | 8 |  | 8020 | 4302 | https://8020.net/4302.html |  | $4.41 | $35.28
M6 |  | Bolt assemblies (T-slot) | 56 |  | 8020 | 3320 | https://8020.net/3320.html |  | $0.95 | $53.20 | includes 3330 (5/16-18 x .687" Flanged Button Head Socket Cap Screw (FBHSCS)) and 3278 (5/16-18 Slide-in Economy T-Nut - Offset Thread)
M7 | Y | Bolts (main plate) 5/16-18 x 1" | 8 |  | 8020 | 3118 | https://8020.net/3118.html |  | $0.50 | $4.00
M8 | Y | Nuts | 24 |  | 8020 | 3759 | https://8020.net/search/?q=3759 |  | $0.12 | $2.88
M9 | Y | Bolt 5/16 x 2.25" (sorbent plate) | 8 |  | 8020 | 3947 | https://8020.net/3947.html |  | $0.87 | $6.96
M10 | N | Screen | 1 |  | McMaster | 9230T752 | https://www.mcmaster.com/9230T752 |  | $35.70 | $35.70
M11 | Custom | Aluminum frame | 1 | 14" x 14" x .187" | 8020 | 2454 | https://8020.net/2454.html |  | $61.15 | $61.15 | Back panel (14" x 14"); $28.70 per sq. ft plus $22.09 surcharge per cut piece
M12 | Custom | Sheet metal top | 1 | 24" x 23.75" x 0.125" | 8020 | 2453 | https://8020.net/2453.html |  | $90.33 | $90.33 | Front panel (24" x 23 3/4"); $17.24 per sq. ft plus $22.09 per cut
M13 | Y | Clevis pins | 1 |  | McMaster | 98306A169 | https://www.mcmaster.com/98306a169/ | pack of 25 | $19.50 | $19.50
M14 | N | Silicone joining sealant | 1 |  | McMaster | 7587A25 | https://www.mcmaster.com/7587A25/ |  | $11.98 | $11.98 | May be used to seal the area between screen and 8020 (T-slot) pieces. Other sealants may be acceptable for use

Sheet: Custom parts
Item ID | Description | Material | Fabrication Method | BOM Item ID | Onshape Link | Notes
C1 | Front panel | Aluminum | Laser cutting or machining | M12 | https://cad.onshape.com/documents/3e513bed349fbe5dac3c2097/w/f4ba0cf31e493613401f5693/e/955c0e2c7429b13a7e576c99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 | 3D format in onshape. Part of assembly with C2. 2D with holes is "Front panel with holes". 2D without holes is "Front panel no holes"
C2 | Back panel | Aluminum | Laser cutting or machining | M11 | https://cad.onshape.com/documents/3e513bed349fbe5dac3c2097/w/f4ba0cf31e493613401f5693/e/9d27109c2f5719e474351754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 | 3D format in onshape. Part of assembly with C1. 2D with holes is "Back panel with holes". 2D without holes is "Back panel no holes"
C3 | Sensor box | PLA, other materials acceptable | 3D printing |  | https://cad.onshape.com/documents/c282863293f77fd9e75ee4bd/w/2c50dc42efc36e588e65a721/e/5b92aeb24f4da54017deff87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 | 3D format in onshape. Part of assembly with C4 and C5.STEP and STL formats provided
C4 | Sensor wing 1 | PLA, other materials acceptable | 3D printing |  | https://cad.onshape.com/documents/c282863293f77fd9e75ee4bd/w/2c50dc42efc36e588e65a721/e/efdcb61e3b5e69728ca9ccd4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 | 3D format in onshape. Part of assembly with C3 and C5.STEP and STL formats provided
C5 | Sensor wing 2 | PLA, other materials acceptable | 3D printing |  | https://cad.onshape.com/documents/c282863293f77fd9e75ee4bd/w/2c50dc42efc36e588e65a721/e/b06d98954c317904f2366b7b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 | 3D format in onshape. Part of assembly with C3 and C4.STEP and STL formats provided

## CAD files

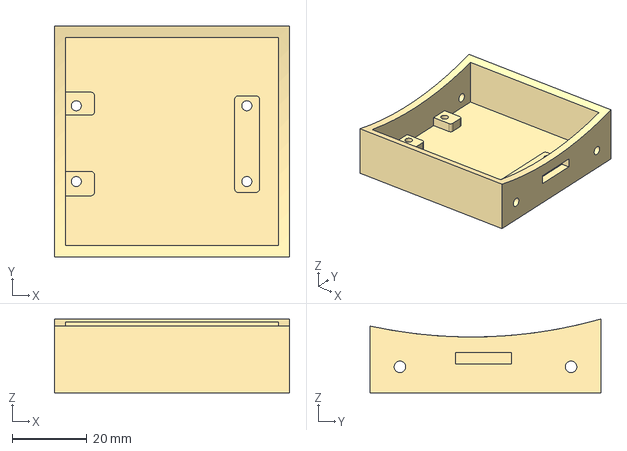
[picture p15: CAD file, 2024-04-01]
hardware_files/CAD/C3_CO2 sensor box.step
63.0 x 61.9 x 19.8 mm

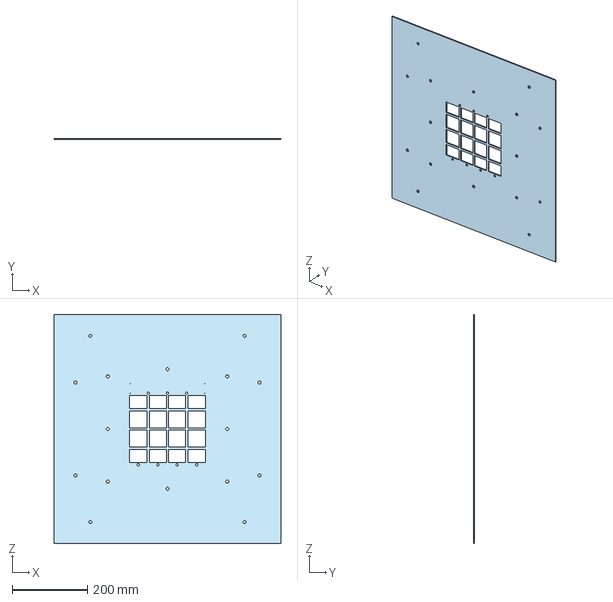
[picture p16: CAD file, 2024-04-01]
hardware_files/CAD/C1_front_panel_custom.step
603.2 x 3.17 x 609.6 mm

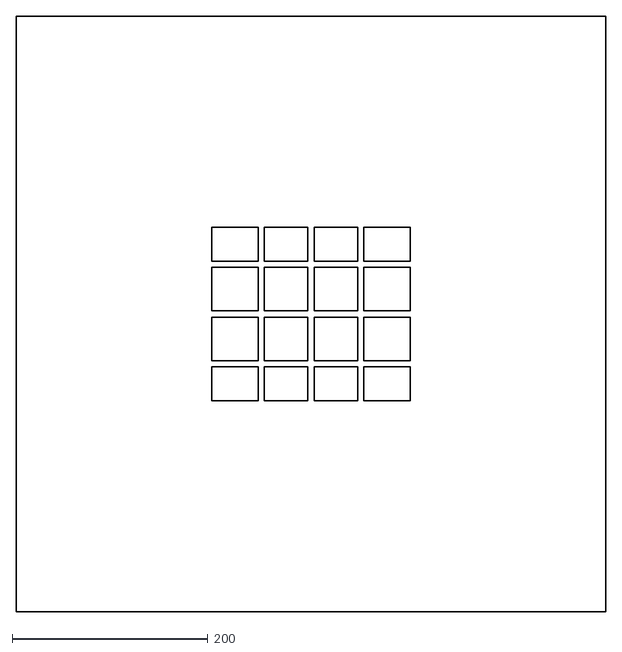
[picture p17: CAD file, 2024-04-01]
hardware_files/CAD/C1_front_panel_custom_no_holes_24in_x_23.75in.dxf
603.2 x 609.6

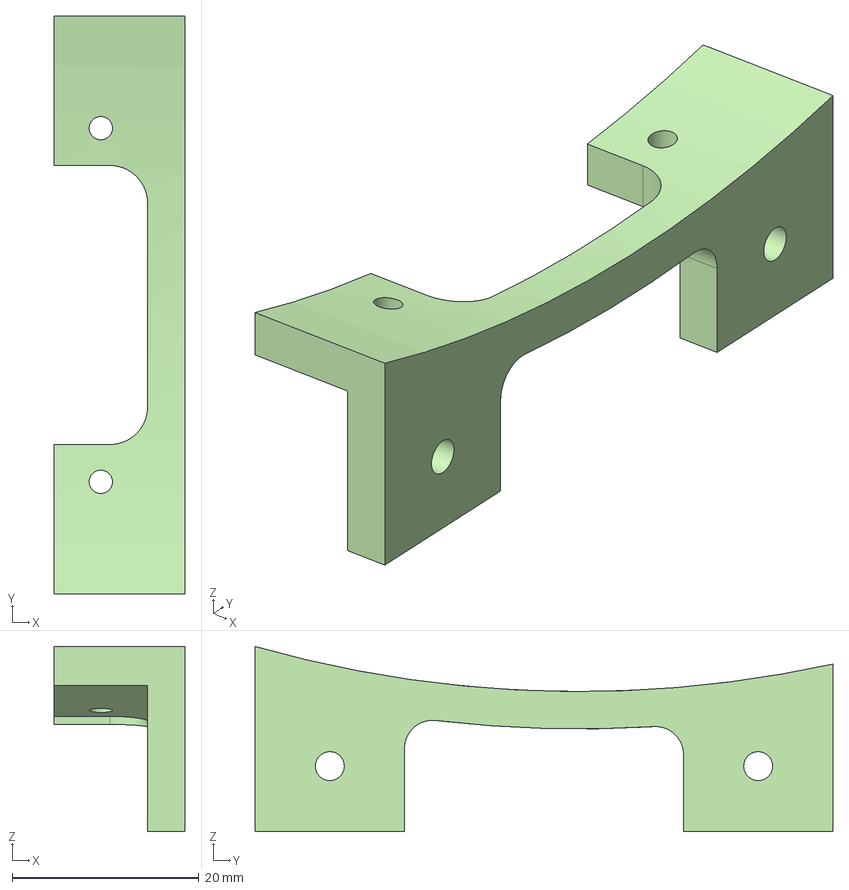
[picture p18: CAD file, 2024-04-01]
hardware_files/CAD/C5_CO2 sensor box wing side 2.step
14.0 x 61.9 x 19.8 mm

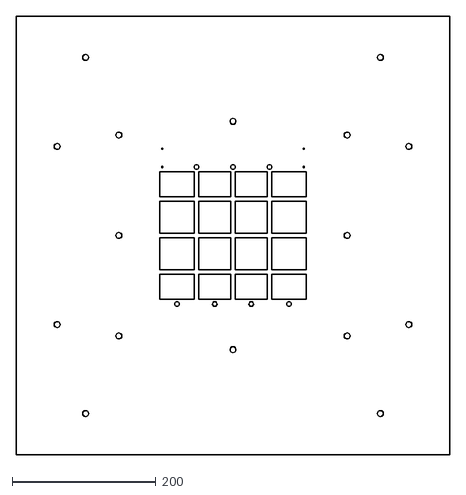
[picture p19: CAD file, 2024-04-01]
hardware_files/CAD/C1_front_panel_custom_with_holes_24in_x_23.75in.dxf
603.2 x 609.6

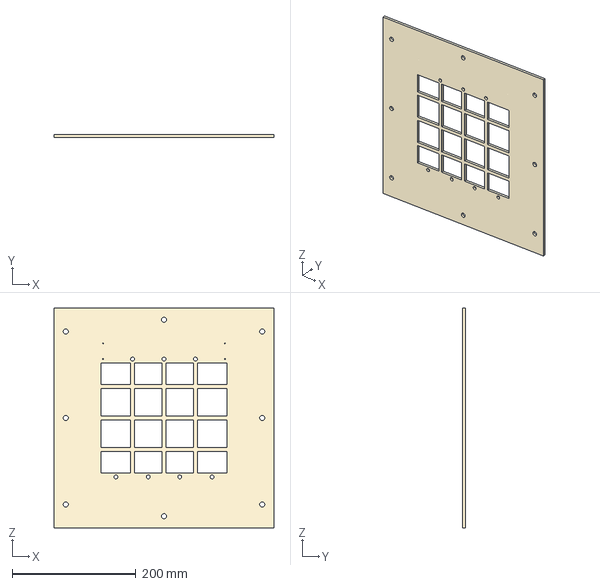
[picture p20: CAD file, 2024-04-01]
hardware_files/CAD/C2_back_panel_custom.step
355.6 x 4.75 x 355.6 mm

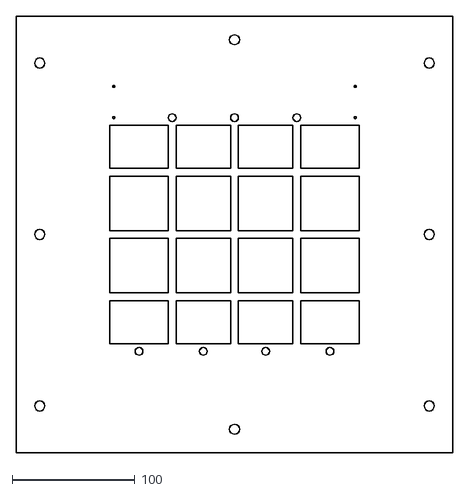
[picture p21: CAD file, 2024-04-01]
hardware_files/CAD/C2_back_panel_custom_with_holes_14in_x_14in.dxf
355.6 x 355.6

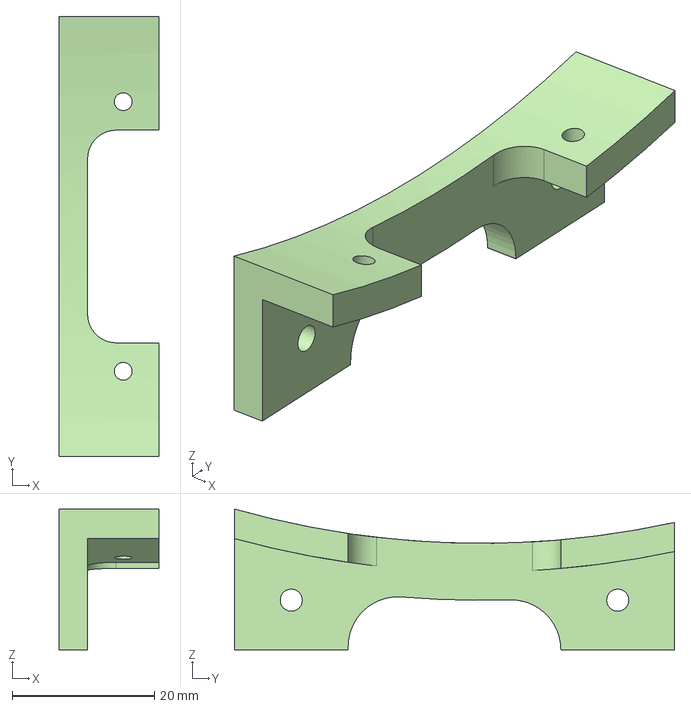
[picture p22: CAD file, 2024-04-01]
hardware_files/CAD/C4_CO2 sensor box wing side 1.step
14.0 x 61.9 x 19.8 mm

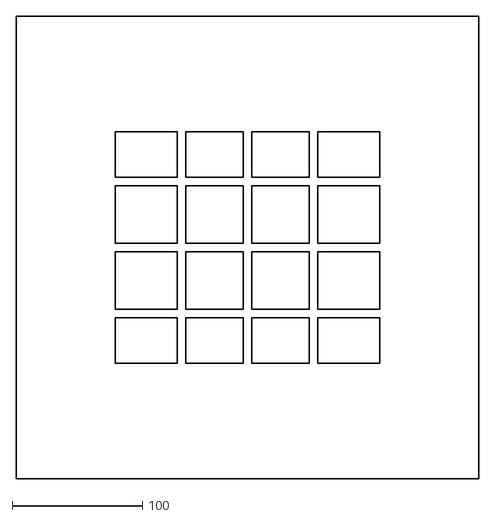
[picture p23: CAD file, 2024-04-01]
hardware_files/CAD/C2_back_panel_custom_no_holes_14in_x_14in.dxf
355.6 x 355.6

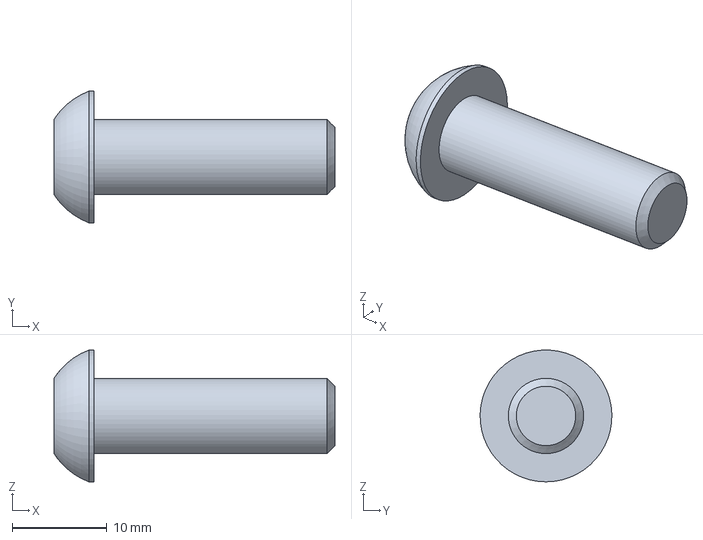
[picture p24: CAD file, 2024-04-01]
hardware_files/CAD/M7_8020_3118_bolt main plate.stp
29.6 x 13.9 x 13.9 mm

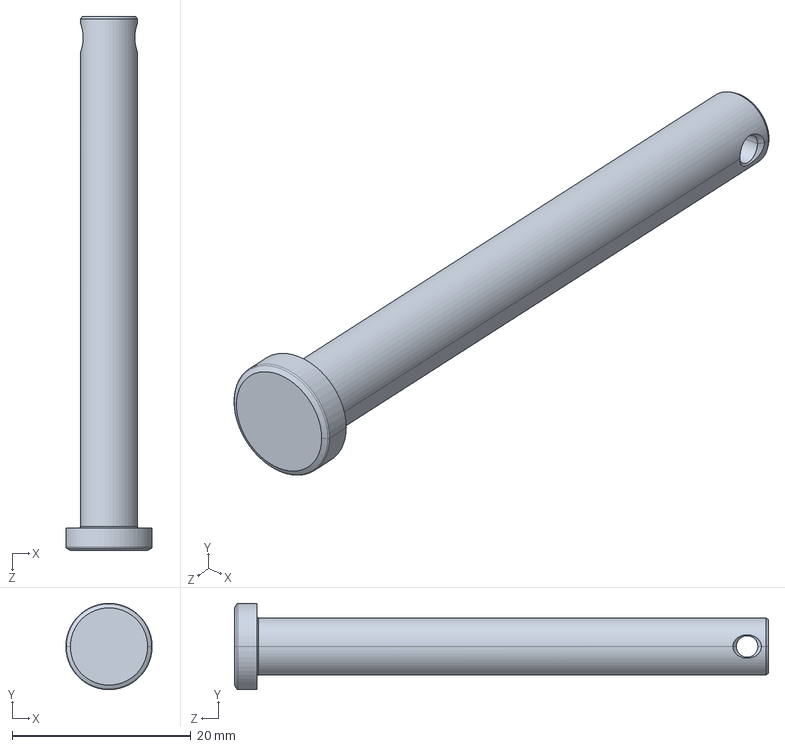
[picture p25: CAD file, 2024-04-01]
hardware_files/CAD/M13_mcmaster_98306A169_Carbon Steel Clevis Pin.STEP
9.65 x 9.65 x 59.7 mm

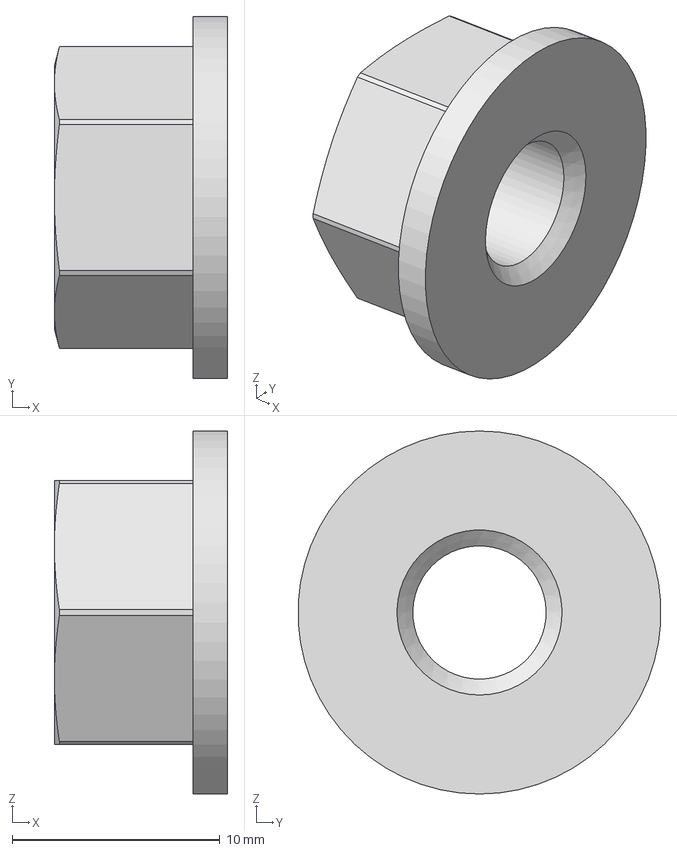
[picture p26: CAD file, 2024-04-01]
hardware_files/CAD/M8_8020_3759_nut.stp
8.33 x 17.4 x 17.5 mm

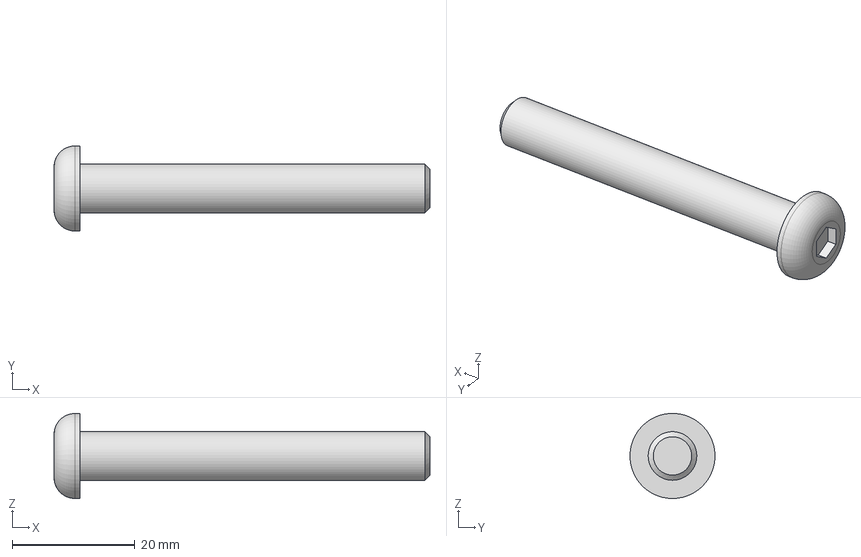
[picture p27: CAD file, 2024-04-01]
hardware_files/CAD/M9_8020_3947_button-head bolt.stp
61.4 x 13.9 x 13.9 mm

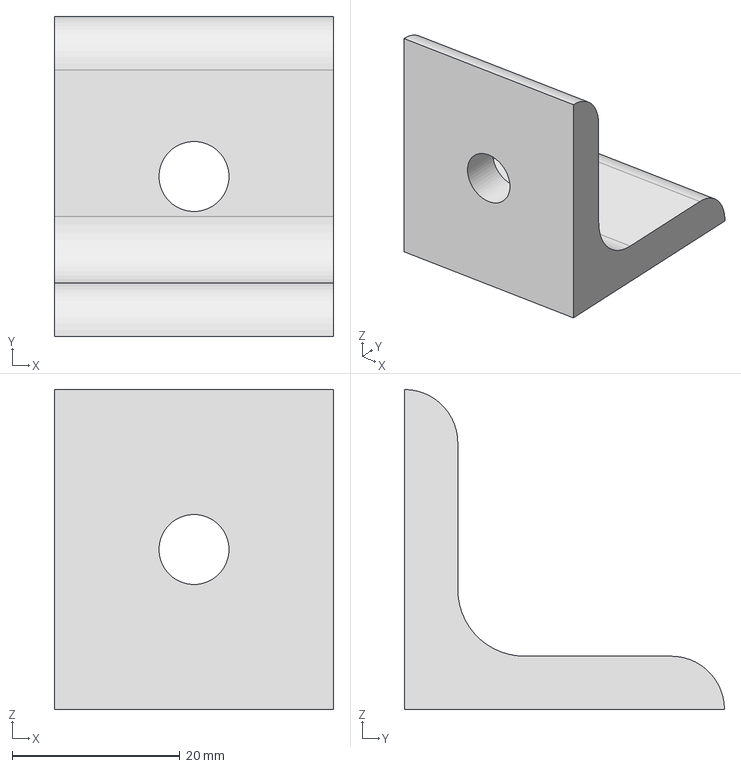
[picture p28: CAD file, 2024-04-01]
hardware_files/CAD/M5_8020_4302_L-bracket.stp
33.3 x 38.1 x 38.1 mm

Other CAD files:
hardware_files/CAD/M1_mcmaster_47065T144_23.75in_T-Slotted Framing.STEP
hardware_files/CAD/M3_mcmaster_47065T144_8in_T-Slotted Framing.STEP
hardware_files/CAD/M2_mcmaster_47065T144_21in_T-Slotted Framing.STEP
hardware_files/CAD/M4_mcmaster_47065T144_2.5in_T-Slotted Framing.STEP
hardware_files/CAD/C3_CO2 sensor box.stl
hardware_files/CAD/C4_CO2 sensor box wing side 1.stl
hardware_files/CAD/C5_CO2 sensor box wing side 2.stl

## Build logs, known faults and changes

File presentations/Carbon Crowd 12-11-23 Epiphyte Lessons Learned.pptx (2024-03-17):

## Project Epiphyte

Lessons Learned
Advice for Next Builder

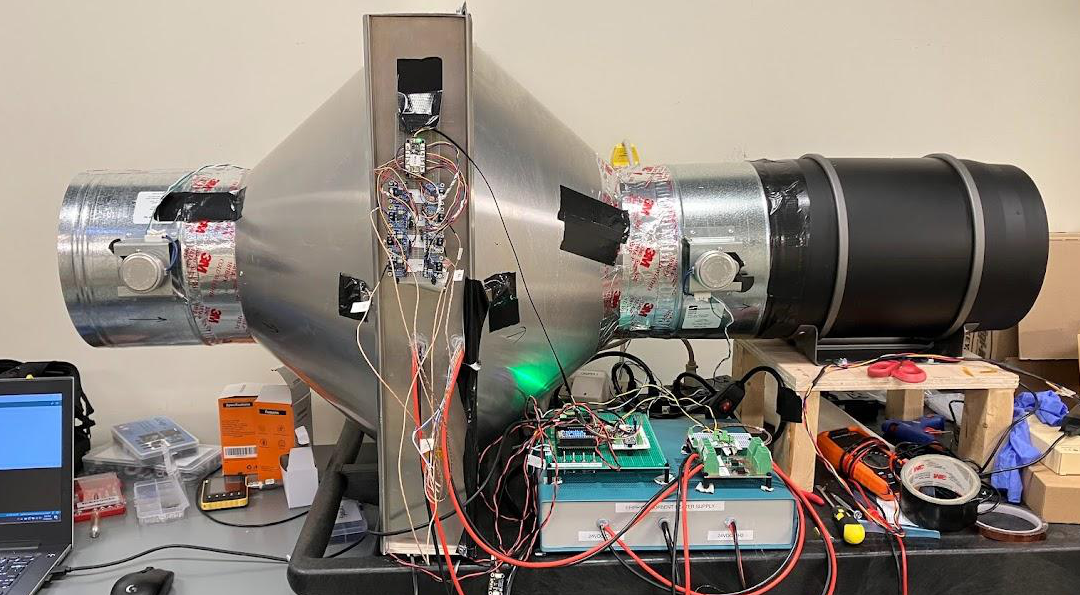
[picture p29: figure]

## Accomplishment: We captured (some) CO2! With a system built by part-time volunteers on a limited budget.

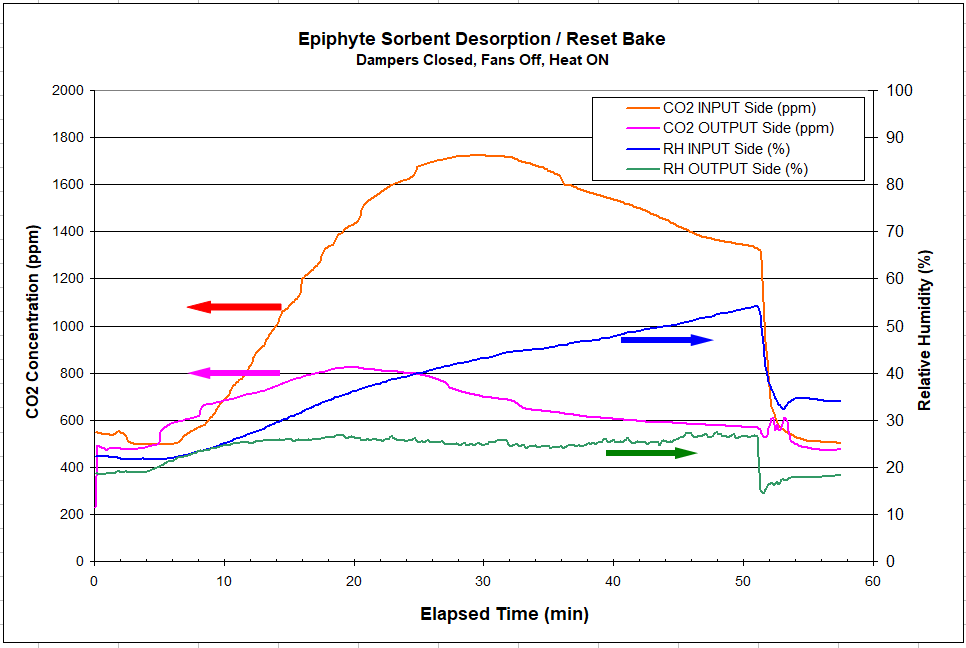
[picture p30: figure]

## A few suggested improvements and advice

## Need Better Sorbent

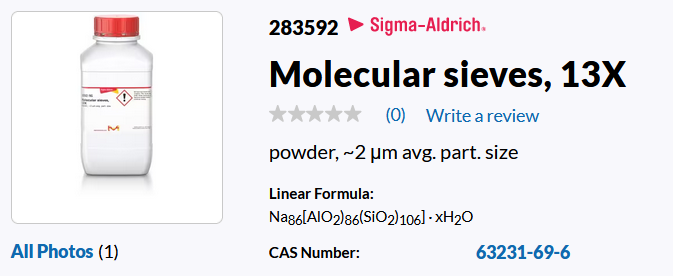
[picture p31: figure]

- Zeolite 13X is NOT ideal for capturing CO2
- Estimated CO2 captured in a 1-hour cycle: Approx. 300mg

## Improve thermal characteristics of sorbent panel

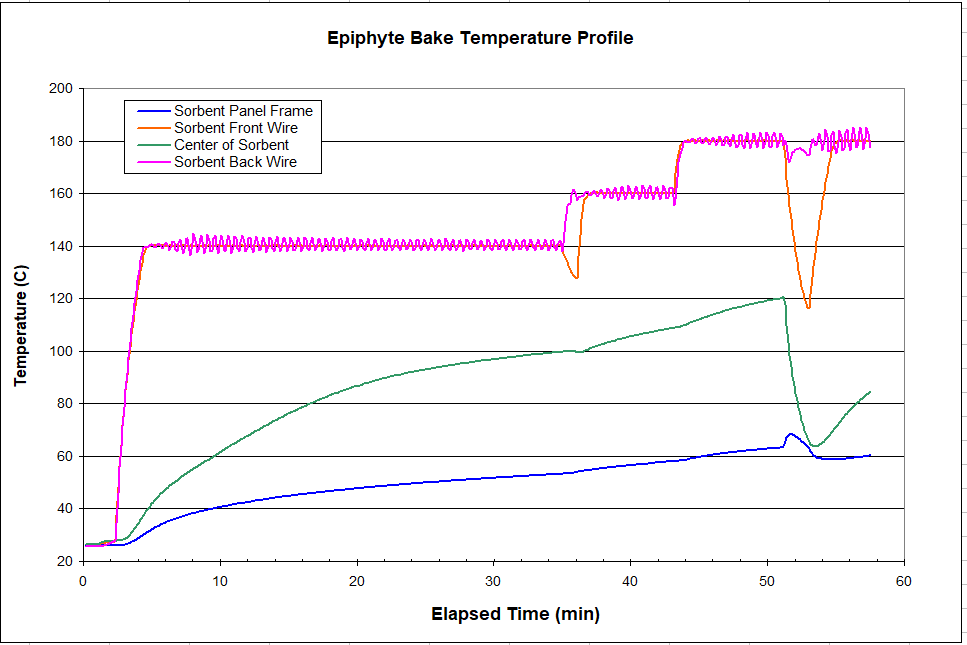
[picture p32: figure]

Lots of metal draws heat away from sorbent

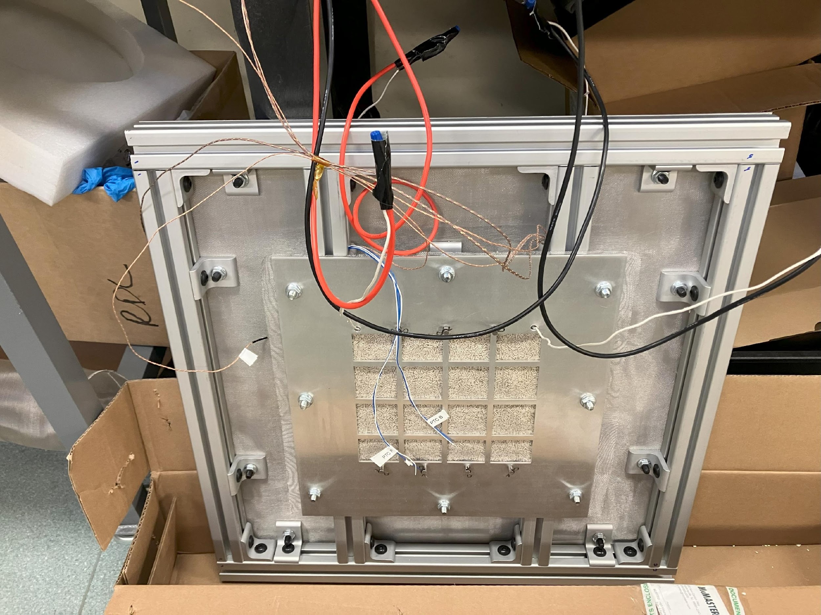
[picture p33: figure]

## Need tighter box for sorbent chamber

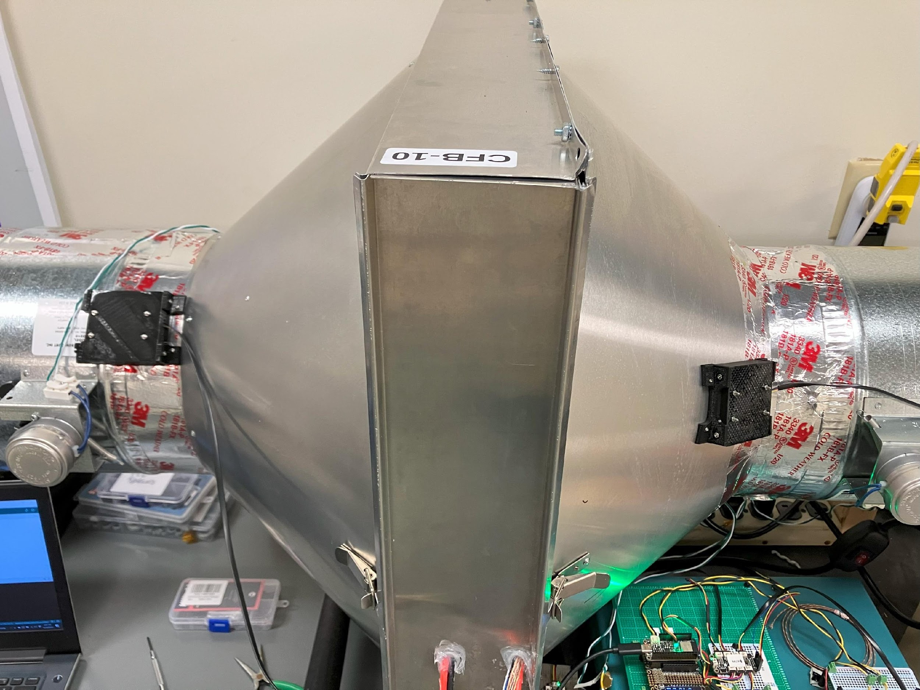
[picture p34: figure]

LEAKY!

FLIMSY!

## Need vacuum-sealing dampers/valves

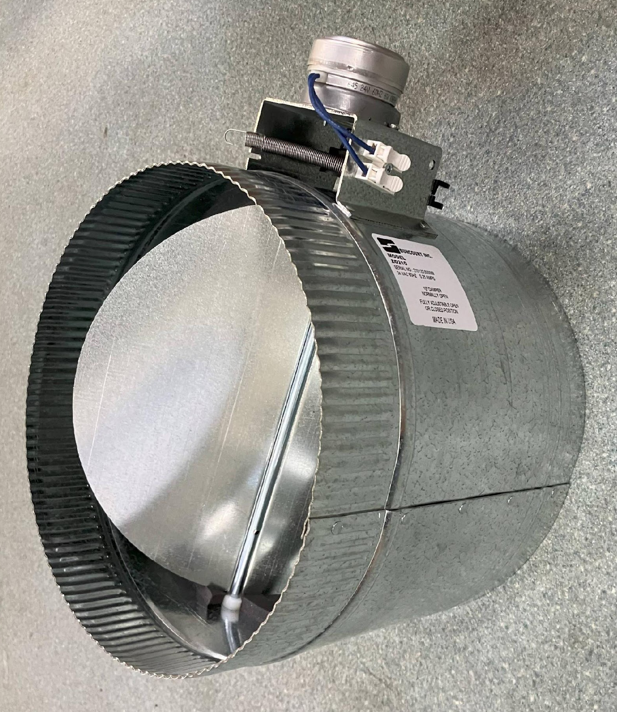
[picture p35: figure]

## CO2 Sensor Issues (Turbulence, Repeatability)

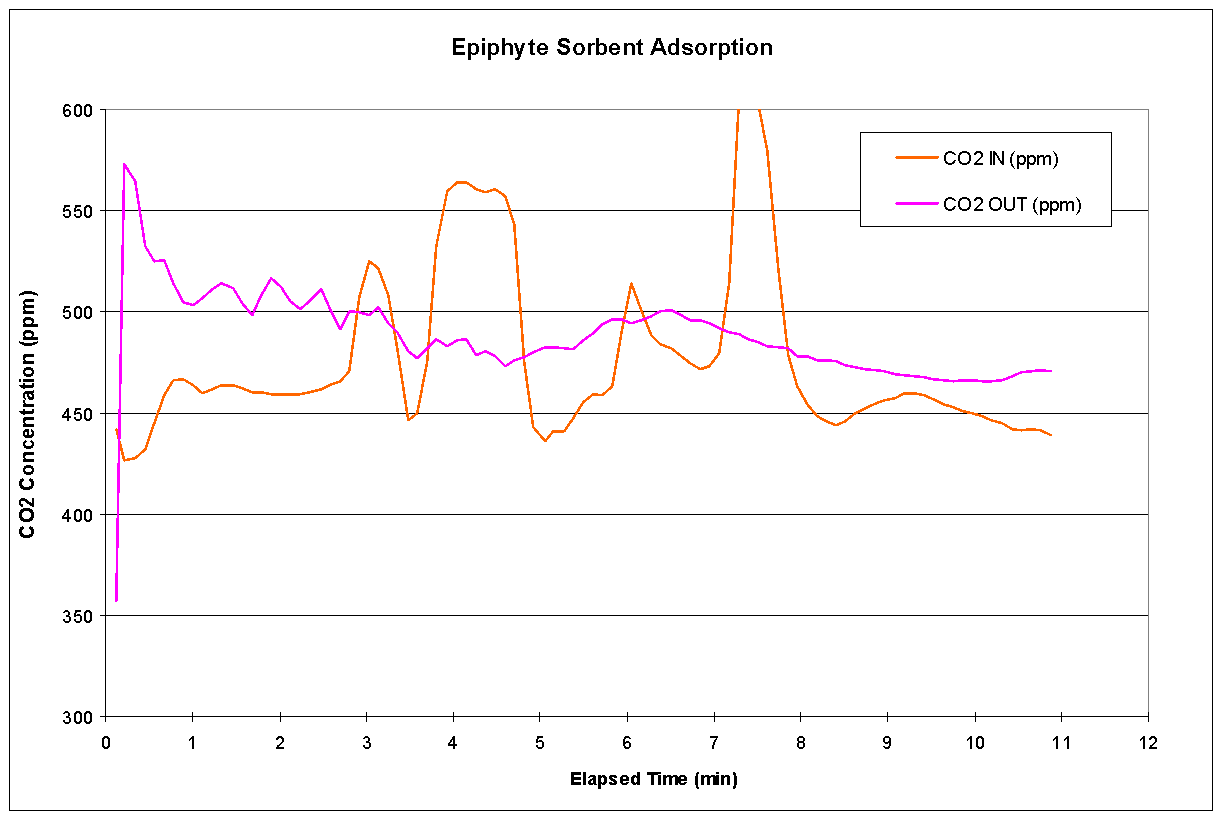
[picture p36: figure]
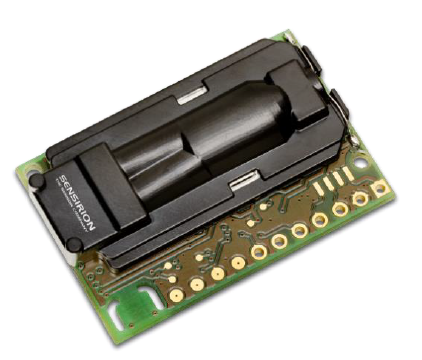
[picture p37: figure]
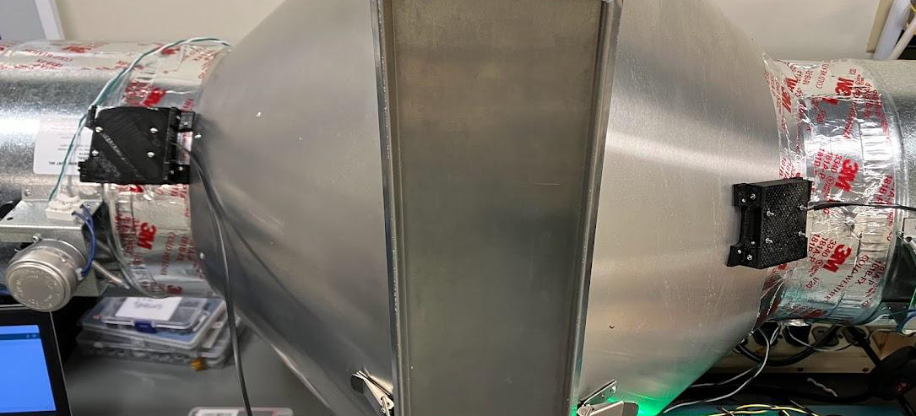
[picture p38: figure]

Need to understand airflow and placement

## Pay Attention to Electronics e.g. CO2 Sensors

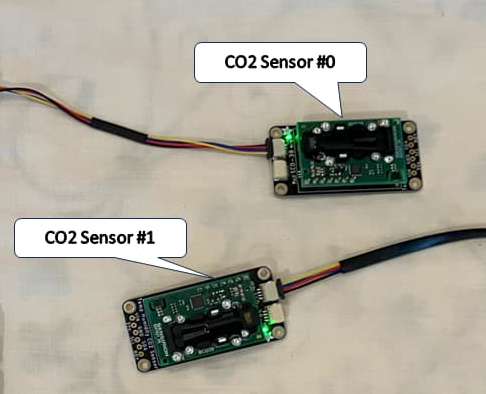
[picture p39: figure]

Original wiring: Adafruit Stemma QT Cables.
Glitchy and missing data!

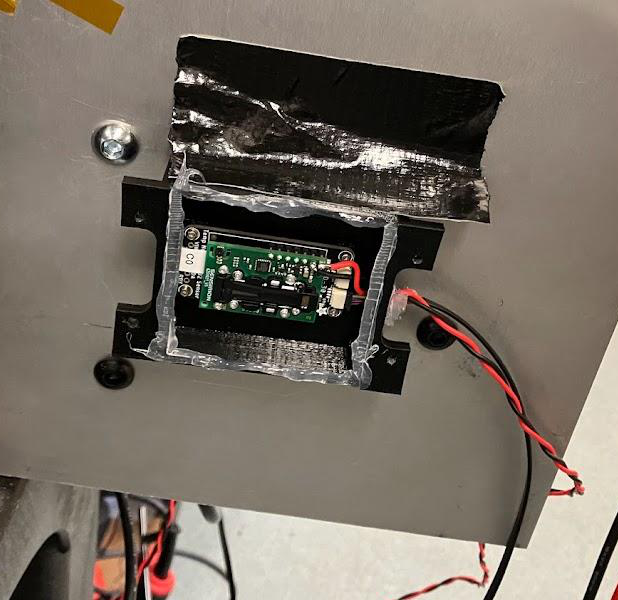
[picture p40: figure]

Improved wiring: Separate power wires, bypass voltage regulator on breakout board

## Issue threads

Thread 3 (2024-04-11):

Educational ready?

dgutson, 2024-04-11:
Hi,

  Is epiphyte ready/mature to be a school project?
If so, could you please give me an estimate of the required budget?

KCollins, 2024-06-03:
Epiphyte isn't yet ready to be an educational project, as it's still in a stage of active development.

We recommend Cyan instead: https://github.com/openair-collective/openair-cyan
At the time of writing, Cyan's not currently being maintained, but can be copied or forked if you would like.

Closed 2024-06-03.

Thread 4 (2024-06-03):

DOC: Add circuit board files to repo.

KCollins, 2024-06-03:
Schematics and board files should be added.

KCollins, 2024-06-03:
@lingxkong - David may have put these files in the Drive.

Closed 2024-08-01.

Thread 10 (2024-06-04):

ENGR: Incorporate vacuum-sealing dampers and valves.

KCollins, 2024-06-04:
The dampers on either end of the sorbent chamber have a critical role to play: sealing off the sorbent chamber from outside air flow, and preventing leaks when the vacuum is applied. The current dampers probably aren’t rated for this use case. We need something more heavy duty.

https://youtu.be/8wVI6kYwSDQ

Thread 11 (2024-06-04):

ENGR: Improve thermal characteristics of sorbent panel

KCollins, 2024-06-04:
Achieving high energy efficiency is critical to arriving at a net-positive emissions balance. If we use too much power, that could overwhelm the climate benefit of removing CO2 with the same device. With the first build a lot of the precious heat generated to desorb the sorbent was absorbed by the metal that makes up the sorbent panel. We need to figure out a way to reduce this “thermal vampirism” so that more heat goes directly to the sorbent.

https://youtu.be/f3UlfJ3lYFI

lingxkong, 2024-06-16:
This idea is unrelated to the metallic construct of the device/sorbent panel frame, and instead, has more to do with the fact that the sorbent 3D footprint is quite thick (1.5 inches). Due to sorbent being a non-conductive material, and a single set of zigzagging wires heating the whole volume, we want to test a thinner slab of sorbent volume without rebuilding the entire sorbent panel construct. Additionally, a thinner slab will reduce the air pass-through resistence through sorbent that may be moderately tightly packed.

The overall idea is to build an insert that can be inserted into the current sorbent compartment that has a screen. Perhaps this frame would be made of wood for easy manufacturability, and also have higher temperature tolerance than plastics (glass transition temperature for some plastics is around 120C), and the screen be mounted in the middle to simply halve the thickness of the sorbent compartment.

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

This wooden frame should have pretty snug fit inside the compartment in all three dimensions to ensure that the sorbent is not migrating to the other half of the compartment, and some adjusting and configurations will be necessary to get this new fixture to play well with the existing clevis pins.

Note that while it would be ideal to make a frame that has an adjustable screen position, this would significantly increase the engineering complexity of such fixture. It is better to make multiple fixtures, such as one that has the screen at the half-way point, resulting in a 0.75 inch thick sorbent compartment, and one that that has the screen at the 0.5 inch mark, engineer it to be flippable/reversible, and therefore capable of testing a 1-inch thick and a 0.5 inch thick compartment.

The last note is on the expansion of the sorbent compartment in the X- and Y- directions (whereas the above idea is regarding the compression of the Z-direction). although it would be ideal to expand the length and width of the sorbent compartment, it would be a complex change and should be a task saved for later. On expansion, multiple pieces of hardware would need to be re-engineered, re-fabricated, and re-configured with no guarantee of new eye-opening learnings (i.e., we know that increasing the window size should increase the capture rate, but that's obvious. We want to learn about the non-obvious if we were to do a re-design and apply all learnings toward the re-design).

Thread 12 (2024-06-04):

ENGR: Upgrade/calibrate CO2 Sensors

KCollins, 2024-06-04:
The CO2 sensors at the air input and within the chamber are critical to measuring if and how much CO2 absorption has occurred per cycle. With our first build the product we used was very difficult to calibrate. To address this problem, we anticipate a sensor swap, but also need to design the chamber for more optimal air flow.

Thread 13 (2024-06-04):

ENGR: CO2 sensors: Decrease turbulence/increase reliability

KCollins, 2024-06-04:
Related to Issue #12 .

With  our CO2 sensors we also experienced a lot of turbulence and noise, making it hard to measure accurately. In addition to a product upgrade we also need to reconsider the  chamber and sorbent panel design design to optimize for smoother air flow, and an alternate method of sheltering the sensor head..

mxbifurcations, 2024-07-05:
I took inspiration from Epiphyte for a slightly different purpose : make a buffering device in a greenhouse heated by a biochar unit. The DAC device in adsorption mode should clip CO2 above 1300ppm and should sustain CO2 level under 600 ppm when in desorption mode. I want to add a parallel pipe to reduce turbulences around the oulet sensor with geotextile layers. I looked at images of CFD for filters but did not perform CFD for this parallel chamber myself.

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

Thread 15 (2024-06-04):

ENGR: Improve/reduce resistance of airflow through sorbent panel

KCollins, 2024-06-04:
Related to Issue #14 .

With our current sorbent panel, the sorbent is tightly packed in to maximize quantity and therefore absorption capacity. But this causes a lot of resistance for airflow, which also has an energy cost. We need to rethink how we can get the same amount or more sorbent ih the device, while also allowing for less resistance.

lingxkong, 2024-06-16:
This is an idea relating to the intrinsic properties of how the sorbents settle based on the way the device is build. The chamber is a rectangular prism slab with the two long sides equal in length, similar to a square drink coaster. The slab sits on one of its thin sides, causing the sorbent to settle down toward the bottom thin side through the force of gravity. This idea has been documented in the[ #epiphyte channel](https://discord.com/channels/656929401933529088/1059420084583546890/1249622156409831457) on the [Open Air discord](https://openaircollective.com/join/).

**Problem it’s supposed to solve:** If the sorbent chamber is not entirely filled, any gaps will cause the air passing through to take the path of least resistance, particularly if the sorbent is powder form rather than pellets. We would like to force a certain amount of air through portions of the sorbent window, particularly at the bottom.

**Description of idea/proposed solution:** It’s a tunnel interfacing the sorbent window with the fan (there is only one fan at the output which pulls air through using negative pressure). The key with this tunnel is that it’s divided up into portions—maybe 4, 9, or 16 divisions so that each division gets its own window of sorbent to work on, i.e., pull air through.

(please excuse the hand-drawn)
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

**Materials:** There is a supplier called TAP Plastics that I have access to. I can’t see why suppliers similar to McMaster would also have plexiglass or polycarbonate pipes, and I believe I have seen square ones. Mounting is a separate issue and I haven’t optimized it in my head—maybe a supporting structure from the bottom, or some L brackets to mount.

**Potential technical difficulties and their workarounds:** I think this idea will by no means go smoothly. I am already worried about implementation

- may need sealing between the sorbent window and the tunnel. May need to create a custom part to do this. This gets mechanically complicated quickly. Not to mention the fan side also.

- If the sorbent is powder, there may be no way to stir up the sorbent and just applying negative pressure will just cause clumping. Is there a way to reverse the fan once in a while? Moving to positive pressure and turning the whole device so that the inlet is at the bottom and outlet is at the top may also help. This is, of course, not easy.

See also [this post](https://github.com/openair-collective/openair-epiphyte/issues/11#issuecomment-2171931588) in issue #11 for another angle for air flow-through.

mxbifurcations, 2024-07-26:
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
A search on "fluidized bed with vortex" shows a variety of designs made to move solid grains in a gas flow. A wood chips / dust collector works the same way. If hot air is blown the chamber could also perform the desorption ?

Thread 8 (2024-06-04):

ENGR: Upgrade sorbent

KCollins, 2024-06-04:
The chemical material that does the work  of absorbing CO2 is called sorbent. For our first build in Philadelphia we used a zeolite-based variety, because it was cheap and available. But it didn‘t perform well, and absorbed more H2O than CO2. So we are seeking alternatives. And in the longterm we see Epiphyte as a platform for test ing and deploying novel sorbents.

https://youtu.be/91708kTRDvE

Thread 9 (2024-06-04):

ENGR: Make sorbent chamber airtight/vacuum grade

KCollins, 2024-06-04:
To maximize the carbon desorption efficiency and speed we need to integrate a vacuum pump with Epiphyte, and plan to do so for build 2. However, our initial design will need to be upgraded to ensure sufficient chamber thickness and durability, and we also need to make it completely air tight and leak free for it to work. So changes to the chamber are in the works.

https://youtu.be/0Ex-jDHngww

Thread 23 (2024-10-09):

Search for a fan of the right size without heat tolerance

lingxkong, 2024-10-09:
Preferably varying speed controlled by arduino or similar. The diameter of the fan should be around 8 inches, to be mounted to the outside of the chamber, so there is some flexibility with this dimension.

Closed 2024-11-07.

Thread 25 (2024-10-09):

Explore mounting of heat resistant fan inside chamber

lingxkong, 2024-10-09:
We need to arrive at a decision on how to mount a fan for distributing heat around the chamber. If mounting safely is not possible, we would need to look into using an oven fan.

Samparets, 2024-11-14:
We are planning on using a funnel on each side of the fan. The funnel will sit on brackets and we can epoxy between the funnel and the inner wall of the chimney. The fan will sit between the two funnels and we can use epoxy to seal between the fan and the two funnels.

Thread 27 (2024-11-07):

Wash coat trial monoliths

Tempo7581, 2024-11-07:

Aaron-T-A, 2024-11-13:
Using the newer, shorter chain PEI we just recieved

penguins4u2, 2024-11-21:
1st batch of monoliths were received  11/14 from Alibaba. These monoliths are made of mostly cordierite (not pure alumina, Al2O3) and are NOT of the right hole density.

Aaron-T-A, 2025-02-07:
One of these monoliths has been put in an Ethanol solution, but it seems to have retained a lot of the ethanol in the monolith as it was cool to the touch even after having dried out for some time.

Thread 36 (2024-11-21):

Prepare PEI-Silica wash coat solutions

penguins4u2, 2024-11-21:
*waiting on information for procedure from Kersh (associate from Clarity Tech)*

Need:

- **Develop scaled up procedure (how much PEI, Silica gel, water needed?)**
- 3x buckets (at least ~gallon)

Have:

- DI water
- Silica powder (SiO2 powder from lab, 5 kg)
- PEI (800 mw and 24,000 mw, large and small chain PEI)

Aaron-T-A, 2025-02-07:
For PEI Solution, we need:
- Ethanol
- PEI (shorter chain)
- Cover for Home Depot Buckets (not necessary, but could slow down evaporation of ethanol)

Planning to test this with both the Alibaba and Clarity Tech monoliths after they have been shaped before expanding to both monoliths

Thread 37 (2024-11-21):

Items for Sequestration Research from Will's Lab

kavyaashah, 2024-11-21:
- DI water (1 liter)
- Graduated Cylinder (that can measure up to 100 ml)
- A scale
- A pH probe (if possible, if not we can try using pH paper)

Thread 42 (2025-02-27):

Make Simple Sensor Readers

KaytchJam, 2025-02-27:
Make simple Arduino readers to acquire Humidity data, Temperature data, and CO2 data. With said data, produce 3 graphs per phase (where our phases are Absorption and Desorption). The graphs will all be <data> * time graphs.

KaytchJam, 2025-03-01:
Wrote `raw_co2_reader.ino` for temperature & co2 sensor readings. Couldn't find humidity sensor in the BOM so leaving it for now.

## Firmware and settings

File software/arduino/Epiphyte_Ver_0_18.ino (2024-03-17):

/*********************************************************************
* Project Epiphyte DAC System Control Program
* OpenAir Collective
* David Wilson dw@ieee.org
**********************************************************************
* Version 0.6: Add structure to provide flexible number and types
*   of sensors.
* Version 0.7: Clean up output routines. 
* Version 0.8: Add Renesas FS1015 airflow sensor
* Version 0.9: Add timestamp (hours since start, in lieu of RTC)
* Version 0.9: Add PWM for controlling heater
* Version 0.10: Add switch debouncing and other features to make set/run robust
* Version 0.11: Add PWM control for second heater
* Version 0.12: Add PID temperature control for sorbent heaters
* Version 0.13: Various improvements to PID control
* Version 0.14: Replace "velocity" form of PID eqn with "positional" form
* Version 0.15: Add limits to integrated error err_int
* Version 0.16: Updates to CO2 sensor
* Version 0.17: Debug CO2 sensors
* Version 0.18: Clean up for Github
*********************************************************************/
/*********************************************************************
 * IMPORTANT:
 * This software is written for the Adafruit ESP32 Feather V2 and has
 * not been tested on any other processor. Product page:
 *              https://www.adafruit.com/product/5400
 * Be sure to follow instructions on loading drivers and adding board
 * to the Board Manager. Make sure correct board is selected in IDE.
 * Make sure all libraries are installed. One must be edited (below)
*********************************************************************/
#define VERSION "0.18"

#include <Arduino.h>
#include <Adafruit_NeoPixel.h>
#include <Wire.h>
#include <SensirionI2cScd30.h>
#include <Adafruit_GFX.h>
#include <Adafruit_SH110X.h>
#include <Adafruit_I2CDevice.h>
#include <Adafruit_I2CRegister.h>
#include "Adafruit_MCP9600.h"
#include "Adafruit_MPRLS.h"
#include <SparkFun_FS3000_Arduino_Library.h> //NOTE: must edit library header file to set I2C address:
                                             //  #define FS3000_DEVICE_ADDRESS 0x50     

// USER OPTIONS
#define SCD30_MEAS_INTERVAL_SECS  2
#define DISP_UPDATE_INTERVAL_SECS 6
#define PRINT_TIMESTAMP           1   //Set nonzero to print timestamp with data 
#define PRINT_SCD30_RAW           0   //Set nonzero to print raw SCD30 data

//Pin assignments
#define NEOPIXEL_PIN  0
#define swRUN         12  //Toggle switch 
#define swSET         13  //Toggle switch
#define BUTTON_C      14  //Not currently used
#define BUTTON_A      15  //Not currently used
#define HEAT_PWM_1    27    
#define BUTTON_B      32  //Not currently used
#define HEAT_PWM_2    33    

#define MPRLS_RESET_PIN  -1  // set to any GPIO pin # to hard-reset on begin()
#define MPRLS_EOC_PIN    -1  // set to any GPIO pin to read end-of-conversion by pin

#define PWM_CHANNEL_1 0
#define PWM_CHANNEL_2 2 //Recommendation in app note https://esphome.io/components/output/ledc.html
#define PWM_RESOLUTION  14
#define PWM_FREQ     1000
#define PROC_CLOCK  80000000
#define MAX_PWM_DC  95  //Maximum duty cycle in percent (circuits seem to get hot if it's 100%)
#define MIN_PWM_DC  0   //Minimum duty cycle in percent

#define MAX_TEMP_C  200

//I2C Addresses
#define MUX0        0x70  //Not currently used
#define MUX1        0x71  //I2C MUX address
#define MUX2        0x72  //I2C MUX address
#define DISPADDR    0x3C
#define THERMADDR   0x67 

#define GREEN   0,255,0
#define BLUE    0,0,255
#define RED     255,0,0
#define YELLOW  127,127,0

//Constructors for libraries
SensirionI2cScd30 scd30;
Adafruit_SH1107 display = Adafruit_SH1107(64, 128, &Wire);
Adafruit_NeoPixel pixel(1, NEOPIXEL_PIN, NEO_GRB + NEO_KHZ800);
Adafruit_MCP9600 therm;
Adafruit_MPRLS press = Adafruit_MPRLS(MPRLS_RESET_PIN, MPRLS_EOC_PIN);
FS3000 fs;

//Main State Machine
enum State {STATE_UNK, STATE_SET, STATE_RUN};

enum sensorTypes {SCD30, THERM, PRESS, FLOW};
enum print {NOPRINT, PRINT};
enum disp {NODISP, DISP};
enum read {NOREAD, READ};

struct devices {
  uint8_t type;           //Refer to sensorTypes enums
  const char *label;      //Will appear in print or disp
  uint8_t muxAddr;        //I2C address of MUX switch
  uint8_t muxChan;        //MUX channel used
  uint8_t devAddr;        //Device I2C address; can use 0 if built-in to library
  uint8_t ifPrint;        //NOPRINT or PRINT
  uint8_t ifDisp;         //NODISP or DISP
  uint8_t ifRead;         //NOREAD or READ
};

/* Fill in this structure in correct format for each device.
*  Setting NOREAD for unused devices saves cycles and allows more frequent
*  read of other devices.
*  Note: SCD30 REQUIRES THREE CONTIGUOUS LINES!
*  Note: don't remove or comment out any of the thermistors through Th5
*  or the heater control loop won't work. This is a bug that needs to be fixed. */
struct devices dev[] = {
  THERM, "Th0", MUX2, 0, THERMADDR, NOPRINT,    NODISP,   NOREAD,
  THERM, "Th1", MUX2, 1, THERMADDR, PRINT,  NODISP,   NOREAD,
  THERM, "Th2", MUX2, 2, THERMADDR, PRINT,  NODISP,   NOREAD,
  THERM, "Th3", MUX2, 3, THERMADDR, PRINT,    DISP,   READ,
  THERM, "Th4", MUX2, 4, THERMADDR, PRINT,  NODISP, READ,
  THERM, "Th5", MUX2, 5, THERMADDR, PRINT,  DISP, READ,
  THERM, "Th6", MUX2, 6, THERMADDR, PRINT,  NODISP, NOREAD,
  THERM, "Th7", MUX2, 7, THERMADDR, PRINT,  NODISP, NOREAD,
  SCD30, "C0 ", MUX1, 3, 0, PRINT, DISP, READ,   //SCD30: Line 1 of 3
  SCD30, "T0 ", MUX1, 3, 0, PRINT, NODISP, READ,   //SCD30: Line 2 of 3
  SCD30, "H0 ", MUX1, 3, 0, PRINT, NODISP, READ,  //SCD30: LIne 3 of 3
  SCD30, "C1 ", MUX1, 4, 0, PRINT, DISP, READ,  //SCD30: Line 1 of 3
  SCD30, "T1 ", MUX1, 4, 0, PRINT, NODISP, READ,  //SCD30: Line 2 of 3
  SCD30, "H1 ", MUX1, 4, 0, PRINT, NODISP, READ,   //SCD30: LIne 3 of 3 
//  PRESS, "P0 ", MUX1, 5, 0, PRINT, NODISP, READ,
  FLOW,   "F0 ", MUX1, 2, 0, PRINT, DISP,  NOREAD,
  FLOW,   "F1 ", MUX1, 1, 0, PRINT, DISP, NOREAD, 
};

#define NDEVS (sizeof dev / sizeof (struct devices))

struct devdata {float meas; uint16_t nave; uint8_t ispresent;} data [NDEVS];

struct pidParm {
  uint8_t devIndex; //Index of sensor providing feedback from dev[] BE CAREFUL!
  uint8_t pwmIndex; //Index of PWM channel controlled by this loop
  uint16_t dT;      //Delta T in millisec
  float Kp;         //Proportional constant in % of duty cycle / temperature error in C
  float Ki;         //Integral constant in [%/(C * sec)]
  float Kd;         //Derivative constant in [(% * sec)/C]
};
struct pidParm pidParm[] = {  //Fill the structure, one line for each loop
  5, PWM_CHANNEL_1, 1000, 10.0, 1.0, 20.0, 
  3, PWM_CHANNEL_2, 1000, 10.0, 1.0, 20.0,
};

#define NLOOPS (sizeof pidParm / sizeof (struct pidParm))

struct pidData {
  uint8_t enabled;
  uint32_t lastTime;
  float setPt;      //Desired temperature in C
  float err_tk;     //Most recent error in C
  float err_tkm1;   //Previous error in C
  float err_int;    //Integral of all previous errors
  float utk;        //Calculated value for PWM duty cycle (update each time through)

} pidData[NLOOPS];

static uint8_t modeState = STATE_UNK;
uint32_t avgStartTime, sessionStartTime;
static char errorMessage[128];
static int16_t error;

uint8_t prompt;
float dutyPct1, dutyPct2;
float err, setTemp;
const uint16_t dutyMax = (uint16_t) (pow(2, PWM_RESOLUTION) - 1);

uint8_t initPWM (uint8_t chan, uint8_t pin, uint32_t freq, uint8_t resolution)
{
  if (chan > 15) {
    Serial.print("initPWM: Illegal channel number ");Serial.println(chan);
    return(1);
  }
  if (freq * dutyMax > PROC_CLOCK) {
    Serial.print("initPWM: Freq ");Serial.print(freq);Serial.println(" is too high for resolution");
    return(2);
  }
  ledcSetup(chan, freq, resolution);
  ledcAttachPin(pin, chan);
  ledcWrite(chan, 0);
  return(0);
}

void setPWM (uint8_t chan, float dutyPct)
{
  uint16_t dutyBits  = dutyPct * dutyMax / 100.0;
/*  Serial.println("Setting up PWM:");
  Serial.print(" Pct=");Serial.print(dutyPct,4);
  Serial.print(" Bits=");Serial.println(dutyBits); */
  ledcWrite(chan, dutyBits);
}

void initDevs (struct devices dev[], struct devdata data[], uint8_t n) 
{
  uint8_t nDevsActive = 0;
  Serial.print("NDEVS=");Serial.println(n);
  for (uint8_t i = 0; i < n; i++) {
    Serial.print("Device index ");Serial.print(i);Serial.print(" Type ");Serial.print(dev[i].type);Serial.print(" Label ");Serial.println(dev[i].label);    
  }
  for (uint8_t i = 0; i < n; i++) {
    Serial.print("Device index ");Serial.print(i);Serial.print(" Label ");Serial.println(dev[i].label);
    switch(dev[i].type) {
      case SCD30: {
        CO2SensorInit(dev[i], &data[i], SCD30_MEAS_INTERVAL_SECS);
        Serial.print("CO2SensorInit completed for device ");Serial.println(dev[i].label);
        data[i+2].ispresent = data[i+1].ispresent = data[i].ispresent;
        i += 2;
        break;
      }
      case THERM: {
        initTherm(dev[i], &data[i]);
        break;
      }
      case PRESS: {
        initPressure(dev[i], &data[i]);
        break;
      }
      case FLOW: {
        initFlow(dev[i], &data[i]);
        break;
      }
      default: {
        Serial.print("Device ");Serial.print(i);Serial.println(": Type not found.");
        data[i].ispresent = 0;
        break;
      }
    }
    data[i].nave = 0;
    Serial.print("Initialization completed for device ");Serial.println(dev[i].label);
  }
}

void initTherm (struct devices d, struct devdata *data) 
{       
  muxselect(d.muxAddr, d.muxChan);
  if (! therm.begin(d.devAddr)) {
    Serial.print("Thermistor ");Serial.print(d.label);Serial.println(" not found!");
    data->ispresent = 0;
  } else {
  Serial.print("Thermistor ");Serial.print(d.label);Serial.println("  found!");
  data->ispresent = 1;
  therm.setADCresolution(MCP9600_ADCRESOLUTION_18);
  therm.setThermocoupleType(MCP9600_TYPE_K);
  therm.setFilterCoefficient(3);
  therm.enable(true); 
  }
}

void initPressure (struct devices d, struct devdata *data) 
{      
  muxselect(d.muxAddr, d.muxChan);
  if (! press.begin()) {
    Serial.print("Pressure sensor ");Serial.print(d.label);Serial.println(" not found!");
    data->ispresent = 0;
  } else {
    Serial.print("Pressure sensor ");Serial.print(d.label);Serial.println("  found!"); 
    data->ispresent = 1;
  }
}

void initFlow (struct devices d, struct devdata *data) 
{      
  muxselect(d.muxAddr, d.muxChan);
  if (! fs.begin()) {
    Serial.print("Flow sensor ");Serial.print(d.label);Serial.println(" not found!");
    data->ispresent = 0;
  } else {
    Serial.print("Flow sensor ");Serial.print(d.label);Serial.println("  found!"); 
    fs.setRange(AIRFLOW_RANGE_7_MPS);
    data->ispresent = 1;
  }
}

float readTherm (struct devices d) 
{   
  muxselect(d.muxAddr, d.muxChan);
  //Serial.print(d.label);Serial.print(" Hot Junction: ");
  float temp = therm.readThermocouple();
  /*Serial.print(temp,1);
  Serial.print(" Cold Junction: ");
  Serial.println(therm.readAmbient(), 1); */
  return temp;
}

float readPressure (struct devices d)  //Reads MPRLS Pressure Sensor i, returns hPa
{     
  muxselect(d.muxAddr, d.muxChan);
  float p = press.readPressure();
  //Serial.print(d.label);Serial.print(" Pressure: ");
  //Serial.print(p,1); Serial.println(" hPa");
  return (p);
}

float readFlow (struct devices d)  //Reads Flow Sensor i, returns m/s
{     
  muxselect(d.muxAddr, d.muxChan);
  float p = fs.readMetersPerSecond();
  //Serial.print(d.label);Serial.print(" Pressure: ");
  //Serial.print(p,1); Serial.println(" hPa");
  return (p);
}

void initPID(struct pidParm p[], struct pidData d[], uint8_t n ){
  for(uint8_t i=0; i<n; i++) {
    d[i].enabled = 0;
    d[i].setPt = 25;
    d[i].err_tk = d[i].err_tkm1 = d[i].err_int = 0.0;
    d[i].utk = 0;
  }
}

float nextDC(struct pidParm p, struct pidData *d, float err) {    //Calculates next value of duty cycle for PWM loop
  d->err_tkm1 = d->err_tk;
  d->err_tk = err;
  float errIntMax = (MAX_PWM_DC - p.Kp * err) * 1000.0 / (p.Ki * p.dT);
  float errIntMin = (MIN_PWM_DC - p.Kp * err) * 1000.0 / (p.Ki * p.dT);
  d->err_int += err;
  if (d->err_int > errIntMax) {
    d->err_int = errIntMax;
  } else if (d->err_int < errIntMin) {
    d->err_int = errIntMin;
  }
  float utk =  (p.Kp * d->err_tk) + (p.Ki * d->err_int * p.dT / 1000.0) + (p.Kd * (d->err_tk - d->err_tkm1) * 1000.0 / p.dT) ;
  if (utk > (float) MAX_PWM_DC) {
    utk = MAX_PWM_DC;
  }
  if (utk < 0.0) {
    utk = 0.0;
  }
  //Serial.print(" ErrIntMin=");Serial.print(errIntMin,2);Serial.print(" ErrIntMax=");Serial.print(errIntMax,2);
  d->utk = utk;
  return utk;
}

void setPID(struct pidData *data, float t, uint8_t en ){     //Sets temperature goal and enables PWM loop i
  Serial.print("setPID: setPt="); Serial.println(t);
  data->lastTime = millis();
  data->enabled = en;
  data->setPt = t; 
}

void setup() 
{
  uint8_t ret;
  Serial.begin(115200);
  while (!Serial) {
    delay(100);
  }
  Serial.setTimeout(10000UL);

  Serial.print("Welcome to Epiphyte! Version ");Serial.println(VERSION);

  Wire.begin();

  pixel.begin();
  pixel.clear();
  pixel.setPixelColor(0, pixel.Color(YELLOW)); 
  pixel.show();

  pinMode(swRUN, INPUT_PULLUP);
  pinMode(swSET, INPUT_PULLUP);
  pinMode(BUTTON_A, INPUT_PULLUP);
  pinMode(BUTTON_B, INPUT_PULLUP);
  pinMode(BUTTON_C, INPUT_PULLUP);
  pinMode(NEOPIXEL_I2C_POWER, OUTPUT);
  digitalWrite(NEOPIXEL_I2C_POWER, HIGH);


  delay(250); //Wait for OLED to power up
  display.begin(DISPADDR, true);
  display.display();
  delay(1000);
  display.setRotation(1);
  display.setTextSize(2);
  display.setTextColor(SH110X_WHITE);

  Serial.print(NDEVS); Serial.println(" devices registered");
  Serial.println("Begin Initialization");

  initDevs(dev, data, NDEVS);
  Serial.println("initDevs complete.");

  ret = initPWM(PWM_CHANNEL_1, HEAT_PWM_1, PWM_FREQ, PWM_RESOLUTION);
  ret = initPWM(PWM_CHANNEL_2, HEAT_PWM_2, PWM_FREQ, PWM_RESOLUTION);

  initPID(pidParm, pidData, NLOOPS);

  sessionStartTime = avgStartTime = millis();
}

void loop() 
{
  uint8_t i;
  uint8_t swRunHi, swSetHi, swRunHiLast, swSetHiLast;
  float co2, temp, humid; 
  uint32_t sessionElapsedTime, waitForResponseStart;
  float sessionElapsedTimeHours;
  swRunHi = digitalRead(swRUN);
  swSetHi = digitalRead(swSET);
  if         (~swRunHi && swSetHi) {
              modeState = STATE_RUN;
  } else if (swRunHi  && ~swSetHi) {
              modeState = STATE_SET;
  } else {
              modeState = STATE_UNK;
  }

  switch(modeState) {
    case STATE_RUN: {
      pixel.setPixelColor(0, pixel.Color(GREEN));  
      pixel.show();
      prompt = 1;

      for (i = 0; i< NLOOPS; i++) {     //Loop for pid devices
        if ((millis() > pidData[i].lastTime + pidParm[i].dT ) && (pidData[i].enabled)) {
          float read = readTherm(dev[pidParm[i].devIndex]);
          float err = pidData[i].setPt - read;
          //Serial.print("Loop ");Serial.print(i);Serial.print(" Read=");
          //                Serial.print(read);Serial.print(" err= ");Serial.print(err,4);
          float dc = nextDC(pidParm[i], &pidData[i], err);
          //Serial.print("Loop ");Serial.print(i);Serial.print(" err_int=");Serial.print(pidData[i].err_int);Serial.print(" DC= ");Serial.println(dc,2); 
          setPWM(pidParm[i].pwmIndex, dc);
          pidData[i].lastTime = millis();
        }
      }

      for (i = 0; i < NDEVS; i++) {
        if ((data[i].ispresent) && (dev[i].ifRead)) {
          switch(dev[i].type) {
            case SCD30: {
              if (readSCD30IfReady(dev[i], co2, temp, humid, PRINT_SCD30_RAW )) {
                data[i].nave++;
                data[i+1].nave = data[i+2].nave = data[i].nave;
                data[i].meas += co2;
                data[i+1].meas += temp;
                data[i+2].meas += humid;
              } 
              i += 2;      
              break;
            }
            case THERM: {
              data[i].meas += readTherm(dev[i]);
              data[i].nave++;
              break;
            }
            case PRESS: {
              data[i].meas += readPressure(dev[i]);
              data[i].nave++;
              break;
            }
            case FLOW: {
              data[i].meas += readFlow(dev[i]);
              data[i].nave++;
              break;
            }
          }
        } 
      }
      if (millis() > avgStartTime + DISP_UPDATE_INTERVAL_SECS*1000.0) {
        sessionElapsedTime = millis() - sessionStartTime;
        sessionElapsedTimeHours = (float) sessionElapsedTime / 3600000.0;
        display.clearDisplay();
        display.setCursor(0,0);
        if (PRINT_TIMESTAMP) {Serial.print(60.0 * sessionElapsedTimeHours, 2);Serial.print(" ");}
        for (i = 0; i < NDEVS; i++) {
          if (((dev[i].ifPrint) || (dev[i].ifDisp)) && (data[i].ispresent) && (dev[i].ifRead)) {
            data[i].meas /= data[i].nave;
            if (dev[i].ifPrint) {Serial.print(dev[i].label);Serial.print("=");Serial.print(data[i].meas);Serial.print(" ");}
            if (dev[i].ifDisp) {display.print(dev[i].label);display.print("=");display.println(data[i].meas,2);}
            data[i].meas = 0.0;
            data[i].nave = 0;
          }
        }
        //Serial.print("DC=");Serial.print(pidData[0].utk);Serial.print(", ");Serial.print(pidData[1].utk);
        Serial.println();
        yield();
        display.display();
        avgStartTime = millis();
      } 
          break;
        }
        
    case STATE_SET: {
      pixel.setPixelColor(0, pixel.Color(BLUE)); 
      pixel.show();
      if (prompt) {
        Serial.println("Current Heater Temp Settings, in percent:");
        Serial.print("Heater 1: "); Serial.print(pidData[0].setPt);Serial.println("C");
        Serial.print("Heater 2: "); Serial.print(pidData[1].setPt);Serial.println("C");
        Serial.println("Enter new Heater 1 temperature: (<10 to disable)");
      }
      if (Serial.available() > 0) {
        setTemp = Serial.parseFloat();
        setTemp = (setTemp > MAX_TEMP_C) ? MAX_TEMP_C : setTemp;
        while (Serial.available() > 0) {
          Serial.read();
        }
       // setPID(pidData[0],setTemp, 1 );
        pidData[0].setPt = setTemp;
        if (setTemp < 10.0) {
          pidData[0].enabled = 0;
          setPWM(pidParm[0].pwmIndex, 0.0);
          Serial.println("Heater 1 disabled."); 
        } else {
          pidData[0].enabled = 1;
          Serial.print("Heater 1: Set temp=");Serial.println(pidData[0].setPt);
          pidData[0].utk=pidData[0].err_tk=pidData[0].err_tkm1=pidData[0].err_int=0.0;
        }
        pidData[0].lastTime = millis();


        Serial.println("Enter new Heater 2 temperature: (<10 to disable)");
        while (Serial.available() == 0) {}
        setTemp = Serial.parseFloat();
        setTemp = (setTemp > MAX_TEMP_C) ? MAX_TEMP_C : setTemp;
        while (Serial.available() > 0) {
          Serial.read();
        }
        pidData[1].setPt = setTemp;
        if (setTemp < 10.0) {
          pidData[1].enabled = 0;
          setPWM(pidParm[1].pwmIndex, 0.0);
          Serial.println("Heater 2 disabled."); 
        } else {
          pidData[1].enabled = 1;
          Serial.print("Heater 2: Set temp=");Serial.println(pidData[1].setPt);
          pidData[1].utk=pidData[1].err_tk=pidData[1].err_tkm1=pidData[1].err_int=0.0;
        }
        pidData[1].lastTime = millis();
      }
      prompt = 0;
      break;
    } 

    case STATE_UNK: {
      pixel.setPixelColor(0, pixel.Color(RED)); 
      pixel.show();
      break;
    }
  }

}

/*******************************************************************************
** Functions 
/******************************************************************************/
void muxselect(uint8_t addr, uint8_t chan) 
{
  if (chan > 7) return;
  Wire.beginTransmission(addr);
  Wire.write(1 << chan);
  Wire.endTransmission();
  delay(100); //Allow time for switch
}

/*              My functions using Sensirion's library     (MODIFIED)        
** Refer to Sensirion's copyright notice in the library source files. */
void CO2SensorInit(struct devices d, struct devdata *data, uint16_t interval) 
{
  uint8_t major = 0;
  uint8_t minor = 0;
  muxselect(d.muxAddr, d.muxChan);
  delay(100); //Gives I2C MUX time to switch over
  scd30.begin(Wire, SCD30_I2C_ADDR_61);
  scd30.stopPeriodicMeasurement();
  scd30.softReset();
  delay(2000);
  error = scd30.readFirmwareVersion(major, minor);
  if (error != NO_ERROR) {
    Serial.print("CO2 Sensor #"); Serial.print(d.label); Serial.print(": ");
    Serial.print("Error trying to execute readFirmwareVersion(): ");
    errorToString(error, errorMessage, sizeof errorMessage);
    Serial.println(errorMessage);
    data->ispresent = 0;
    return;
  }
  data->ispresent = 1;
  Serial.print("CO2 Sensor #"); Serial.print(d.label); Serial.print(": ");
  Serial.print("firmware version major: ");
  Serial.print(major);
  Serial.print("\t");
  Serial.print("minor: ");
  Serial.print(minor);
  Serial.println();

  error = scd30.activateAutoCalibration(0);
  if (error != NO_ERROR) {
    Serial.print("Error trying to execute activateAutoCalibration(): ");
    errorToString(error, errorMessage, sizeof errorMessage);
    Serial.println(errorMessage);
    return;
  } else {
    Serial.println("Auto Calibration Disabled");
  }

  error = scd30.startPeriodicMeasurement(0);
  if (error != NO_ERROR) {
    Serial.print("Error trying to execute startPeriodicMeasurement(): ");
    errorToString(error, errorMessage, sizeof errorMessage);
    Serial.println(errorMessage);
    return;
  }

  error = scd30.setMeasurementInterval(interval);
  if (error != NO_ERROR) {
    Serial.print("Error trying to execute setMeasurementInterval(): ");
    errorToString(error, errorMessage, sizeof errorMessage);
    Serial.println(errorMessage);
    return;
  }
}
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

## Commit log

2024-01-18 Rename 8020_3278.zip to Hardware Files/CAD/8020_3278.zip
2024-01-18 Rename BOM/epiphyte BOM.xlsx to Hardware Files/BOM/epiphyte BOM.xlsx
    [epiphyte BOM.xlsx]
2024-01-18 Rename Epiphyte Parts Step AP214.zip to Hardware Files/CAD/Epiphyte Parts Step AP214.zip
2024-03-16 feat: add arduino software
2024-03-17 refactor: rename folders to snake_case
    [epiphyte BOM.xlsx]
2024-03-31 feat: update BOM files
    [BOM for Electrical and HVAC Components.xlsx, BOM for Sorbent Panel and CO2 Sensor Box.xlsx, epiphyte BOM.xlsx]
2024-03-31 feat: add updated CAD files
    [C1_front_panel_custom.step, C1_front_panel_custom_no_holes_24in_x_23.75in.dxf, C1_front_panel_custom_with_holes_24in_x_23.75in.dxf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]
2024-07-31 Update Epiphyte Electronics Description.doc
    Added table for toggle switches, a few photographs, and some more description.

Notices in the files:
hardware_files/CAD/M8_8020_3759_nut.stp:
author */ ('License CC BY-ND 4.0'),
